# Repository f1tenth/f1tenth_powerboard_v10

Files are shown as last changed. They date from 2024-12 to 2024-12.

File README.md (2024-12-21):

# Powerboard v10

This is a repository containing the design files and user manual for the Powerboard v10.

Developed by a collaboration between Ambimat Electronics and the University of Pennsylvania.

To purchase, please order from this link: [Ambimat Electronics Powerboard Purchase Link](https://orders.ambimat.com/product/f1tenth-power-board/).

Please reach out to neel.shah@ambimat.com in case there is any issue with the website.

## Repository layout

### Explanation of important files/folders

- ```Powerboard_v10_1_User_Manual.pdf```: Contains a description of the capabilities of the board. 
  - Relevant to everyone looking to purchase, fabricate, or modify the existing design.
- ```hardware_design_files\```: Folder containing the bill of materials, schematics, PCB layout files for Altium, and manufacturing files (drill data, gerber files, and pick-and-place data).
    - Relevant if you want to get the board fabricated yourself.
- ```mechanical_specifications\```: Folder containing the mechanical drawings.
    - Relevant if you want to design a mount or any physical support for this powerboard.

### File layout
```
.
│   Powerboard_v10_1_User_Manual.pdf
│   README.md
│
├───hardware_design_files
│   │   BOM.xlsx
│   │   schematics.pdf
│   │
│   ├───layout
│   │       1. BD.SchDoc
│   │       2. Input Section.SchDoc
│   │       3. Buck Boost_19V.SchDoc
│   │       4. Buck Boost_12V.SchDoc
│   │       5. Buck_5V1A.SchDoc
│   │       6. Revision History.SchDoc
│   │       AE170_PDU_02.04.PcbDoc
│   │       AE170_PDU_02.04.PrjPcb
│   │
│   └───manufacturingData
│       │   PickAndPlaceData.csv.csv
│       │
│       ├───DrillData
│       │       AE170_PDU_02.04-RoundHoles.TXT
│       │       AE170_PDU_02.04-SlotHoles.TXT
│       │       AE170_PDU_02.04.DRL
│       │       AE170_PDU_02.04.DRR
│       │
│       └───GerberData
│               AE170_PDU_02.04.apr
│               AE170_PDU_02.04.G1
│               AE170_PDU_02.04.G2
│               AE170_PDU_02.04.GBL
│               AE170_PDU_02.04.GBO
│               AE170_PDU_02.04.GBP
│               AE170_PDU_02.04.GBS
│               AE170_PDU_02.04.GD1
│               AE170_PDU_02.04.GM1
│               AE170_PDU_02.04.GTL
│               AE170_PDU_02.04.GTO
│               AE170_PDU_02.04.GTP
│               AE170_PDU_02.04.GTS
│
└───mechanical_specifications
        diagram.DXF
        diagram.pdf
```

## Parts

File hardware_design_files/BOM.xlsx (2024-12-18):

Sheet: BOM_AE170_PDU_02.02
Sr.# | Quantity | Designator | Description | PCB Footprint | Manu Part Number | Manufacturer | Vendor-1 | Vendor-1 Part Number | Vendor-2 | Vendor-2 Part Number
1 | 12 | C1, C11, C19, C21, C24, C28, C36, C38, C41, C43, C45, C49 | CAP CER 0.1UF 100V X7R 0603 | 0603 | CC0603KRX7R0BB104 | YAGEO | DIGIKEY | 311-1523-1-ND | MOUSER
2 | 8 | C2, C3, C6, C7, C34, C35, C44, C48 | CAP CER 10UF 50V X5R 0805 | 0805 | GRM21BR61H106KE43L | Murata Electronics | DIGIKEY | 490-18663-1-ND | FARNELL
3 | 3 | C4, C5, C8 | CAP CER 10000PF 50V X7R 0603 | 0603 | CC0603KPX7R9BB103 | Yageo | DIGIKEY | 311-1572-1-ND | FARNELL
4 | 11 | C9, C10, C12, C17, C18, C26, C27, C29, C51, C52, C53 | CAP CER 47UF 25V X5R 1206 | 1206 | C3216X5R1E476M160AC | TDK Corporation | DIGIKEY | 445-8047-1-ND | FARNELL
5 | 2 | C13, C30 | CAP CER 0.015UF 50V X7R 0603 | 0603 | CL10B153KB8NNNC | Samsung Electro-Mechanics | DIGIKEY | 1276-1277-1-ND | FARNELL
6 | 1 | C14 | CAP CER 6800PF 50V X7R 0603 | 0603 | AC0603KPX7R9BB682 | YAGEO | DIgikey | 13-AC0603KPX7R9BB682CT-ND | Element14
7 | 2 | C15, C32 | CAP ALUM POLY 82UF 20% 35V SMD | 8.3 x 8.3 | 35SVPF82M | Panasonic | DIGIKEY | P16562CT-ND | FARNELL
8 | 1 | C20 | CAP CER 100PF 50V C0G/NP0 0805 | 0805 | 08055A101JAT2A | AVX Corporation | DIGIKEY | 478-1316-1-ND | FARNELL
9 | 1 | C22 | CAP CER 270PF 50V X7R 0603 | 0603 | CC0603KRX7R9BB271 | Yageo | DIgikey | 311-1185-1-ND | Element14
10 | 2 | C23, C40 | CAP CER 1UF 50V X7R 0603 | 0603 | CC0603KRX7R9BB105 | Yageo | DIGIKEY | 311-2082-1-ND | FARNELL
11 | 2 | C25, C42 | CAP CER 47PF 50V X7R 10% 0603 | 0603 | C0603C470K5RAC7867 | KEMET | DIGIKEY | 399-16402-1-ND | FARNELL
12 | 1 | C31 | CAP CER 10000PF 50V X7R 0402 | 0402 | CGA2B3X7R1H103K050BB | TDK Corporation | DIGIKEY | 445-6893-1-ND | FARNELL
13 | 1 | C37 | CAP CER 330PF 50V C0G/NPO 0805 | 0805 | CC0805JRNPO9BN331 | YAGEO | DIgikey | 311-1117-1-ND | Element14
14 | 1 | C39 | CAP CER 82PF 50V C0G/NPO 0603 | 0603 | CC0603JRNPO9BN820 | Yageo | DIGIKEY | 311-1068-1-ND | FARNELL
15 | 1 | C46 | CAP CER 47PF 50V C0G/NP0 0402 | 0402 | CL05C470JB5NNNC | Samsung Electro-Mechanics | DIGIKEY | 1276-1699-1-ND | FARNELL
16 | 1 | C47 | CAP CER 47UF 16V X5R 1210 | 1210 | GRM32ER61C476KE15L | Murata Electronics | DIGIKEY | 490-6539-1-ND | FARNELL
17 | 1 | C50 | CAP CER 0.033UF 10V X7R 0402 | 0402 | GRM155R71A333KA01D | Murata Electronics | DIGIKEY | 490-1315-1-ND | FARNELL
18 | 2 | D1, D3 | DIODE SCHOTTKY 50V 5A SMC | DO214AB | B550C-13-F | Diodes Incorporated | DIGI-KEY | B550C-FDICT-ND | MOUSER
19 | 2 | D2, D4 | TVS DIODE 20VWM 32.4VC DO214AC | DO214AC | SMAJ20CA | Littelfuse Inc. | DIGI-KEY | SMAJ20CALFCT-ND | MOUSER
20 | 2 | D5, D8 | DIODE SCHOTTKY 50V 5A SMC | DO214AB | B550C-13-F | Diodes Incorporated | DIGI-KEY | B550C-FDICT-ND | MOUSER
21 | 4 | D6, D7, D9, D10 | DIODE SCHOTTKY 60V 2A SOD123F | SOD123F | SS26FL | onsemi | DIGI-KEY | SS26FLCT-ND | MOUSER
22 | 6 | FB1, FB2, FB3, FB4, FB5, FB6 | FERRITE BEAD 120 OHM 0805 1LN | 0805 | ABUP00201209121Y00 | Pulse Electronics | Digikey | 553-ABUP00201209121Y00CT-ND
23 | 1 | J1 | CONN HEADER SMD 4POS 2MM | HEADER-4P_2.0MM | B4B-PH-SM4-TB | JST Sales America Inc. | DIGIKEY | 455-B4B-PH-SM4-TBCT-ND | FARNELL | sunrom 6334
24 | 1 | J2 | CONN HEADER SMD 6POS 1MM | HEADER 6P | BM06B-SRSS-TB | JST Sales America Inc. | DIGIKEY | 455-BM06B-SRSS-TBCT-ND | FARNELL
25 | 4 | J3, J4, J5, J6 | EURO BLOCK 2P | HEADER-2P_3.5MM | EBWA-02-A | Adam Tech | DIGIKEY | 2057-EBWA-02-A-ND | FARNELL
26 | 2 | J7, J10 | CONN PWR JACK 2.5X5.5MM SOLDER | TH 3P | PJ-050BH | CUI Inc | DIGIKEY | CP-050BH-ND | FARNELL | sunrom 7070
27 | 1 | J8 | CONN HEADER 9PS 2.54MM | 1x9 2.54MM HEADER |  |  | DIGIKEY |  |  | Local
28 | 1 | J9 | CONN HEADER VERT 4POS 2.5MM | HEADER-4P_2.5MM | B4B-XH-A | JST Sales America Inc. | DIGIKEY | 455-B4B-XH-A-ND | FARNELL | sunrom 5225
29 | 1 | L1 | FIXED IND 3.3UH 14A 8.2 MOHM SMD | 8479 | 7443340330 | Würth Elektronik | Digikey | 732-2165-1-ND
30 | 1 | L2 | FIXED IND 2.2UH 9.7A 14.5MOHM SM | 5553 | SRP5030CA-2R2M | Bourns Inc. | Digikey | SRP5030CA-2R2MCT-ND
31 | 1 | L3 | FIXED IND 10UH 5A 21 MOHM SMD | 12.7 X 12.7 | SRR1208-100ML | Bourns Inc. | Digikey | SRR1208-100MLCT-ND | MOUSER
32 | 3 | LED1, LED2, LED3 | LED BLUE CLEAR 3MM 470NM | 0603 | LB Q39G-L2N2-35-1 | OSRAM Opto Semiconductors Inc | DIGIKEY | 475-2816-1-ND | FARNELL | 1652110
33 | 2 | Q1, Q2 | MOSFET N-CH 30V 22A 6SON | 6-SON | CSD17571Q2 | Texas Instruments | DIGIKEY | 296-37193-1-ND
34 | 2 | Q3, Q7 | MOSFET N-CH 60V 50A 8VSON | 8-VSON | CSD18537NQ5A | Texas Instruments | DIGIKEY | 296-36455-1-ND
35 | 1 | Q4 | MOSFET N-CH 100V 14.4A 6WSON | 6-SON | CSD19538Q2 | Texas Instruments | DIGIKEY | 296-47322-1-ND
36 | 3 | Q5, Q6, Q8 | MOSFET N-CH 60V 60A 8VSON | 8-VSON | CSD18543Q3A | Texas Instruments | DIGIKEY | 296-47321-1-ND
37 | 2 | R1, R14 | RES SMD 2K OHM 5% 1/10W 0603 | 0603 | ERJ-3GEYJ202V | Panasonic | DIGIKEY | P2.0KGCT-ND | FARNELL
38 | 2 | R2, R15 | RES SMD 249K OHM 1% 1/10W 0603 | 0603 | AC0603FR-07249KL | Yageo | DIGIKEY | 13-AC0603FR-07249KLCT-ND | FARNELL
39 | 1 | R3 | RES 42.2K OHM 1% 1/10W 0603 | 0603 | RC0603FR-0742K2L | Yageo | DIGIKEY | 311-42.2KHRCT-ND | FARNELL
40 | 2 | R4, R17 | RES SMD 10 OHM 1% 1/10W 0603 | 0603 | CRCW060310R0FKEA | Vishay Dale | DIGIKEY | 541-10.0HCT-ND | FARNELL
41 | 1 | R5 | RES 453K OHM 1% 1/10W 0603 | 0603 | RC0603FR-07453KL | Yageo | DIGIKEY | 311-453KHRCT-ND | FARNELL
42 | 5 | R6, R9, R19, R22, R28 | RES SMD 10K OHM 5% 1/10W 0603 | 0603 | RC0603JR-0710KL | Yageo | DIGIKEY | 311-10KGRCT-ND | FARNELL
43 | 2 | R7, R20 | RES 93.1K OHM 1% 1/10W 0603 | 0603 | RC0603FR-0793K1L | YAGEO | DIGIKEY | 311-93.1KHRCT-ND | FARNELL
44 | 2 | R8, R21 | RES 23.2K OHM 1% 1/10W 0603 | 0603 | RC0603FR-0723K2L | YAGEO | DIGIKEY | 311-23.2KHRCT-ND | FARNELL
45 | 2 | R10, R23 | RES SMD 20K OHM 5% 1/10W 0603 | 0603 | CRCW060320K0JNEA | Vishay Dale | DIGIKEY | 541-20KGCT-ND | FARNELL
46 | 4 | R11, R13, R24, R26 | RES SMD 100 OHM 1% 1/10W 0603 | 0603 | CRCW0603100RFKEA | Vishay Dale | DIGIKEY | 541-100HCT-ND | FARNELL
47 | 1 | R12 | RES 0.01 OHM 1% 3W 2512 | 2512 | PA2512FKE7T0R01E | YAGEO | DIGIKEY | 13-PA2512FKE7T0R01ECT-ND | FARNELL
48 | 1 | R16 | RES SMD 33.2K OHM 1% 1/10W 0603 | 0603 | ERJ-3EKF3322V | Panasonic Electronic Components | DIGIKEY | P33.2KHCT-ND | FARNELL
49 | 1 | R18 | RES SMD 280K OHM 1% 1/10W 0603 | 0603 | CRCW0603280KFKEA | Vishay Dale | DIGIKEY | 541-280KHCT-ND | FARNELL
50 | 1 | R25 | RES 0.018 OHM 1W 1206 WIDE | 2012 | PRL1632-R018-F-T1 | Susumu | DIGIKEY | PRL1632.018FCT-ND | FARNELL
51 | 1 | R27 | RES 52.3K OHM 1% 1/10W 0603 | 0603 | RC0603FR-0752K3L | YAGEO | DIGIKEY | 311-52.3KHRCT-ND | FARNELL
52 | 3 | R30, R31, R32 | RES 470 OHM 1/10W 5% 0603 SMD | 0603 | RC0603JR-07470RL | YAGEO | DIGIKEY | 311-470GRCT-ND | MOUSER
53 | 2 | SW1, SW2 | SWITCH TOGGLE SPDT 7.5A 125V | E101SYZQE | E101SYZQE | C&K | DIGI-KEY | CKN1519-ND | MOUSER
54 | 2 | U1, U2 | LM5176PWPR | 28-HTSSOP | LM5176PWPR | Texas Instruments | DigiKey | 296-49223-1-ND | Element14
55 | 1 | U3 | IC REG BUCK ADJ 2A SOT583 | SOT-583 | TPS62932DRLR | Texas Instruments | DigiKey | 296-TPS62932DRLRCT-ND | MOUSER
 | 127

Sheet: DNP
Sr.# | Quantity | Designator | Description | PCB Footprint | Manu Part Number | Manufacturer | Vendor-1 | Vendor-1 Part Number | Vendor-2 | Vendor-2 Part Number | Mounting
1 | 2 | C16, C33 | CAP CER 22UF 35V X5R 0805 | 0805 | C2012X5R1V226M125AC | TDK Corporation | DIGIKEY | 445-14428-1-ND | FARNELL |  | DNP
2 | 1 | R29 | RES SMD 0 OHM JUMPER 1/10W 0603 | 0603 | CRCW06030000ZSTB | Vishay Dale | DIGIKEY | 541-2971-1-ND | FARNELL |  | DNP

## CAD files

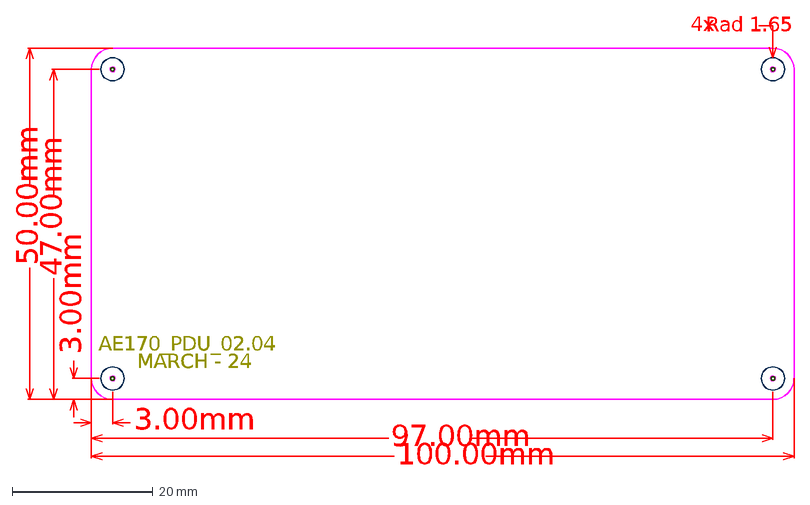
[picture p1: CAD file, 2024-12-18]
mechanical_specifications/diagram.DXF
4x
MARCH - 24
AE170_PDU_02.04
100.00mm
50.00mm
3.00mm
97.00mm
47.00mm
Rad 1.65

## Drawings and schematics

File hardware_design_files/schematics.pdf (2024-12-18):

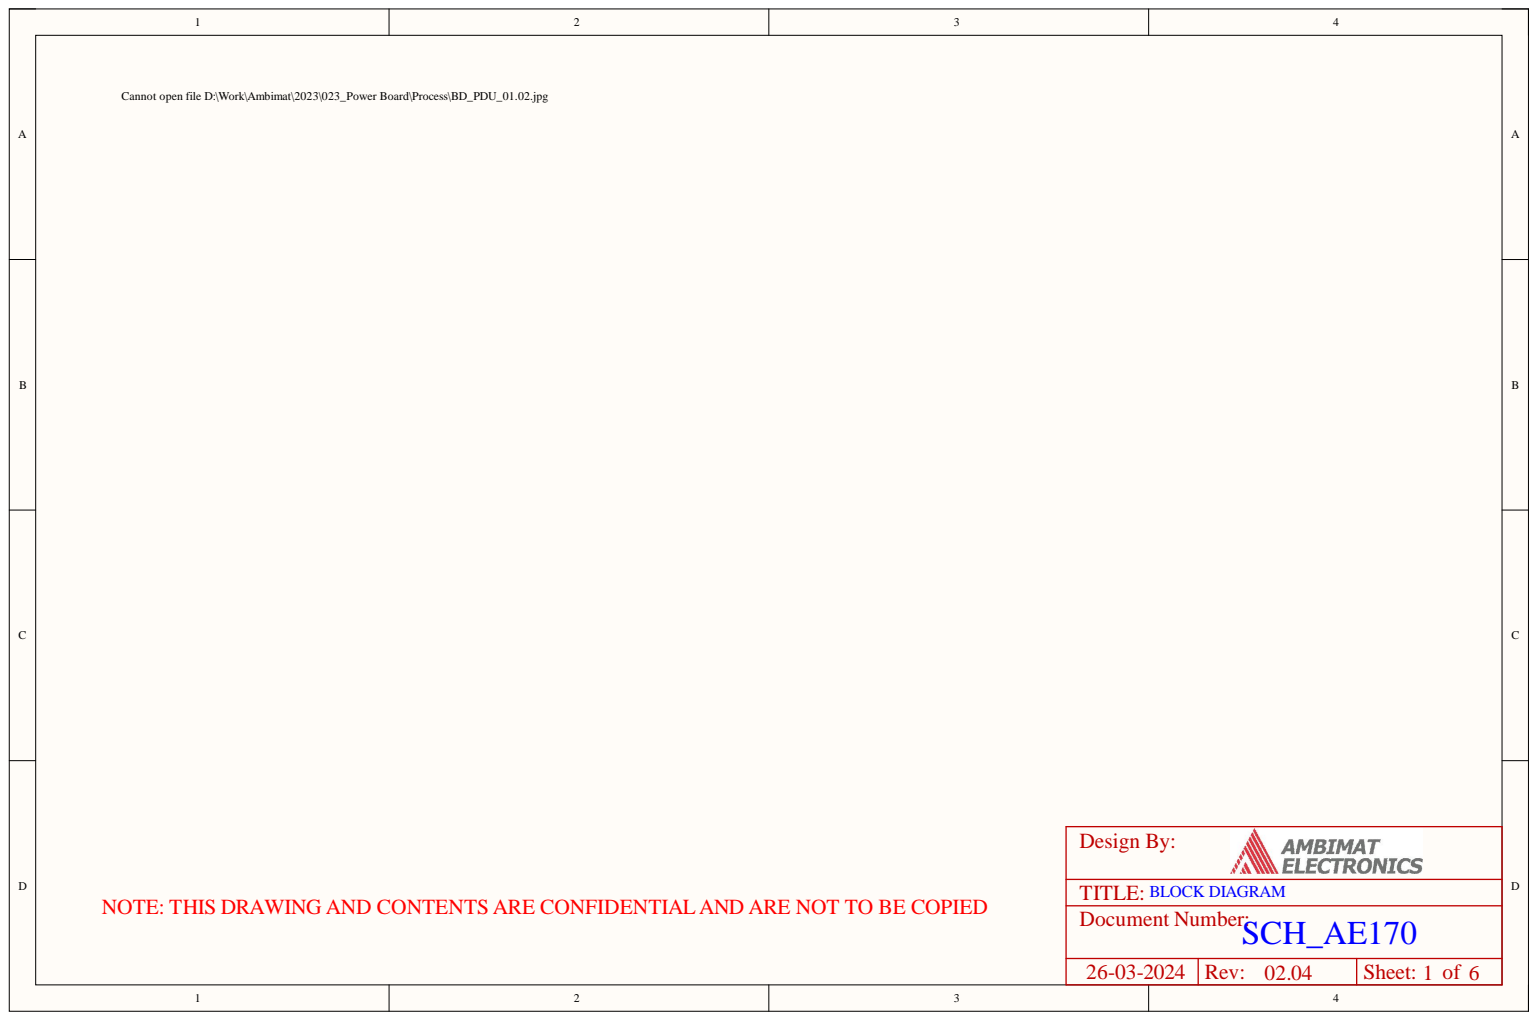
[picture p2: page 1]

Cannot open file D:\Work\Ambimat\2023\023_Power Board\Process\BD_PDU_01.02.jpg

NOTE: THIS DRAWING AND CONTENTS ARE CONFIDENTIALAND ARE NOT TO BE COPIED

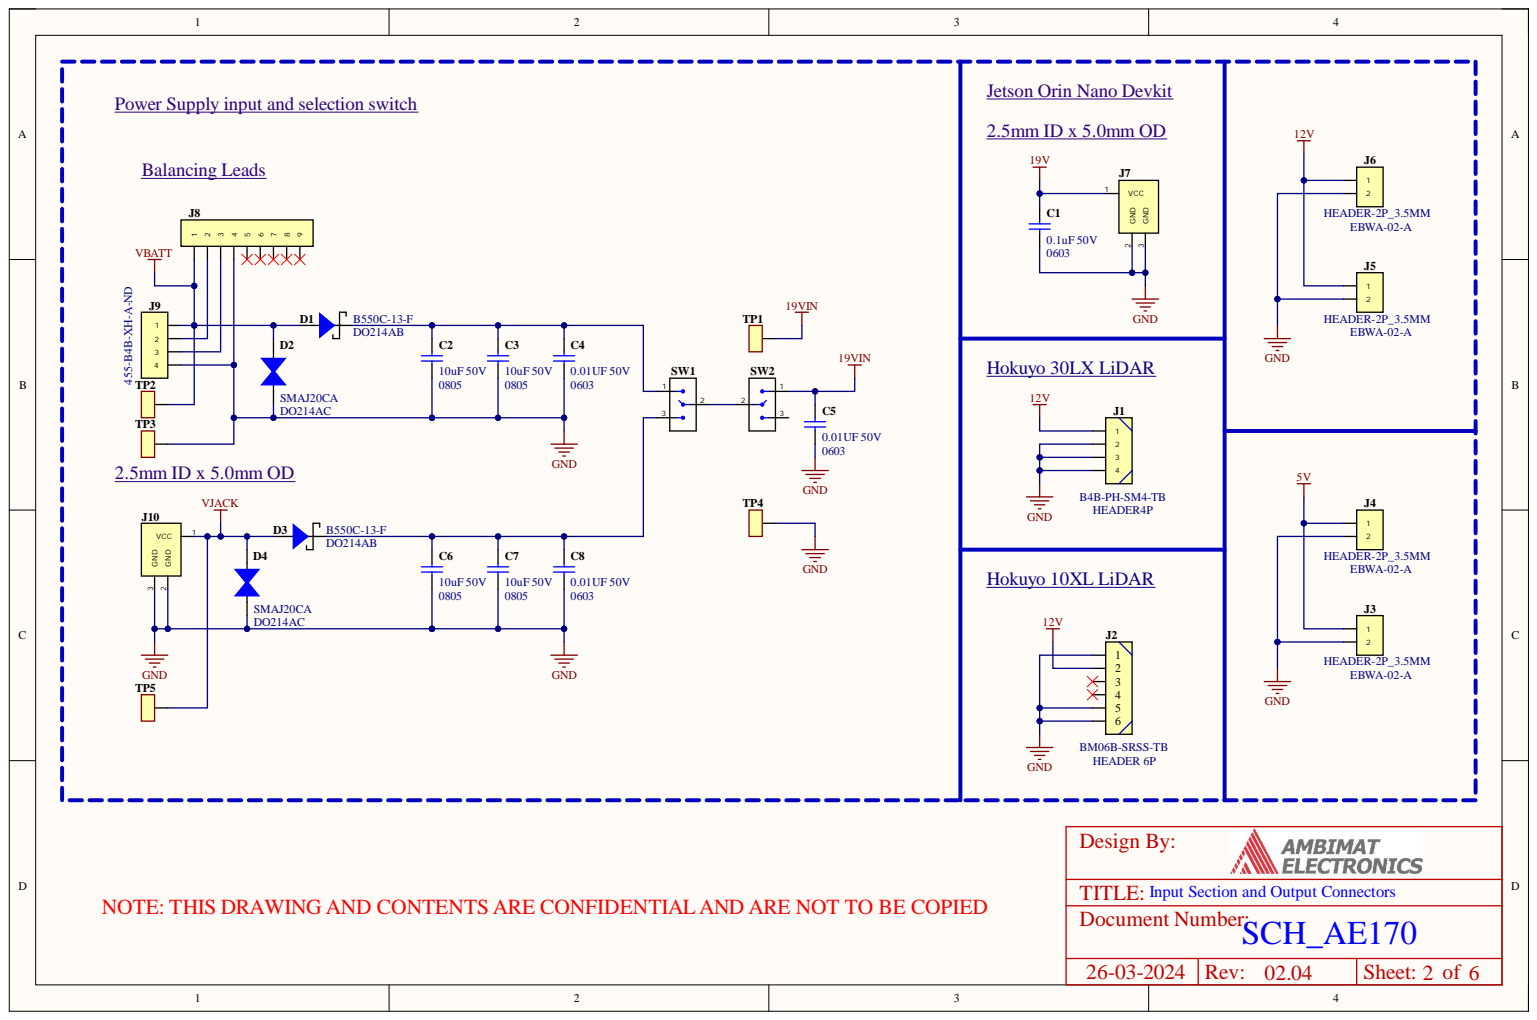
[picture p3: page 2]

ARE NOT TO BE COPIED

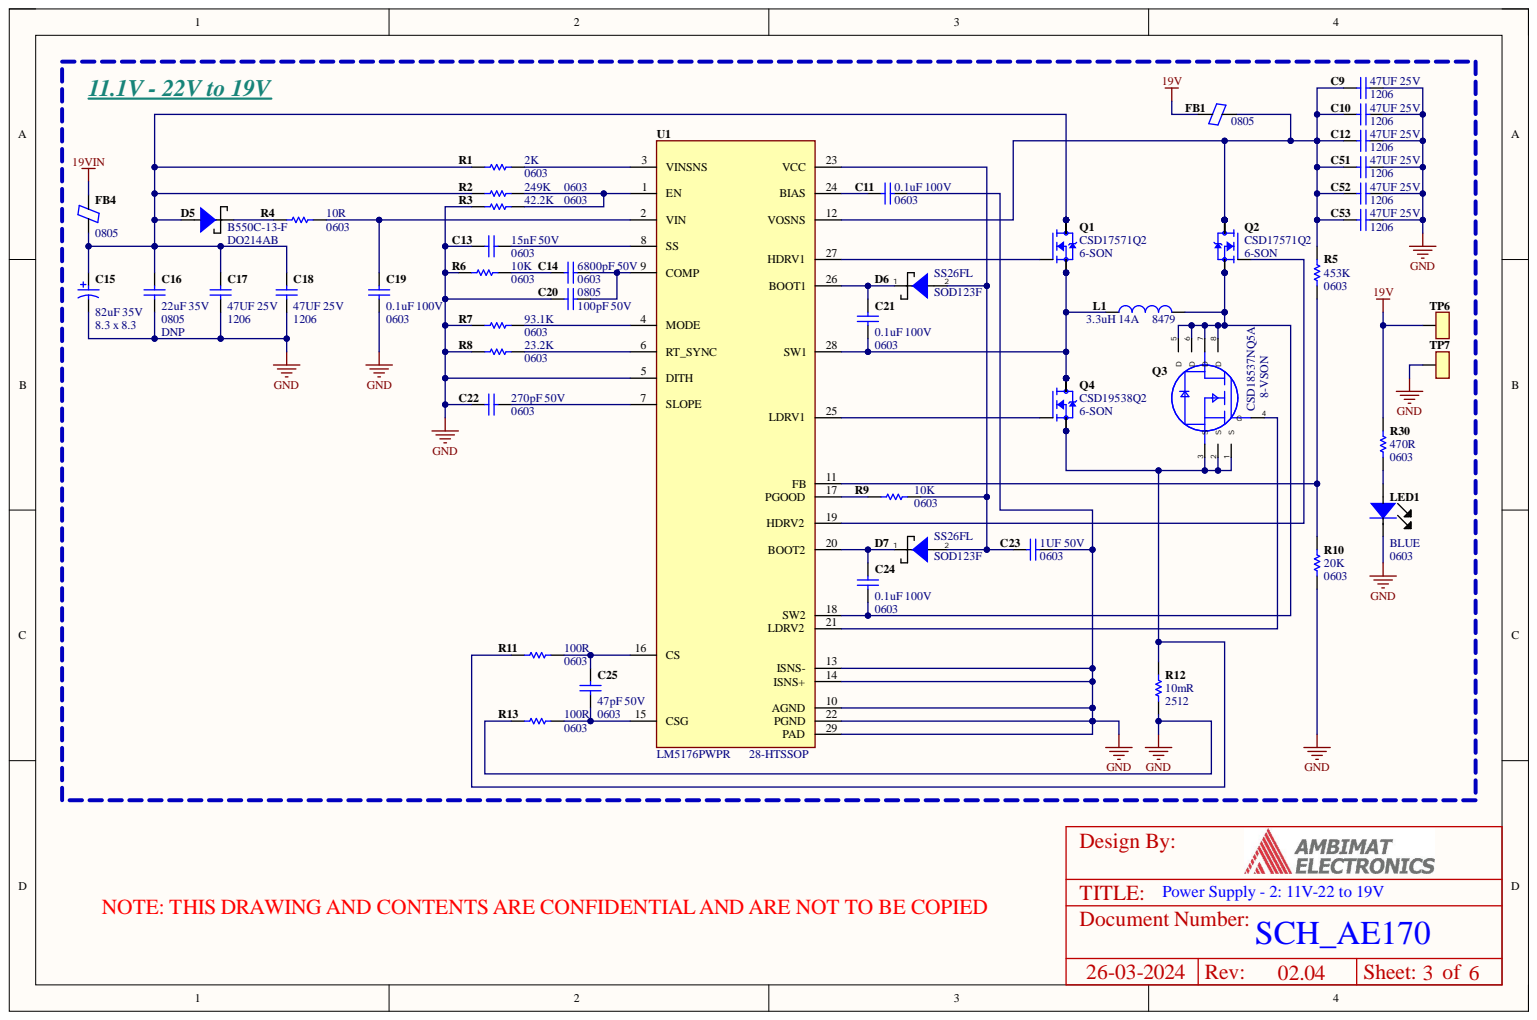
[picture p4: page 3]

2 6
2 8 | | SO D 1 2 3 F

1 1
1 7 | R 9 1 0 K
1 9 | 0 | 6 0 3

1 3
1 4

ARE NOT TO BE COPIED

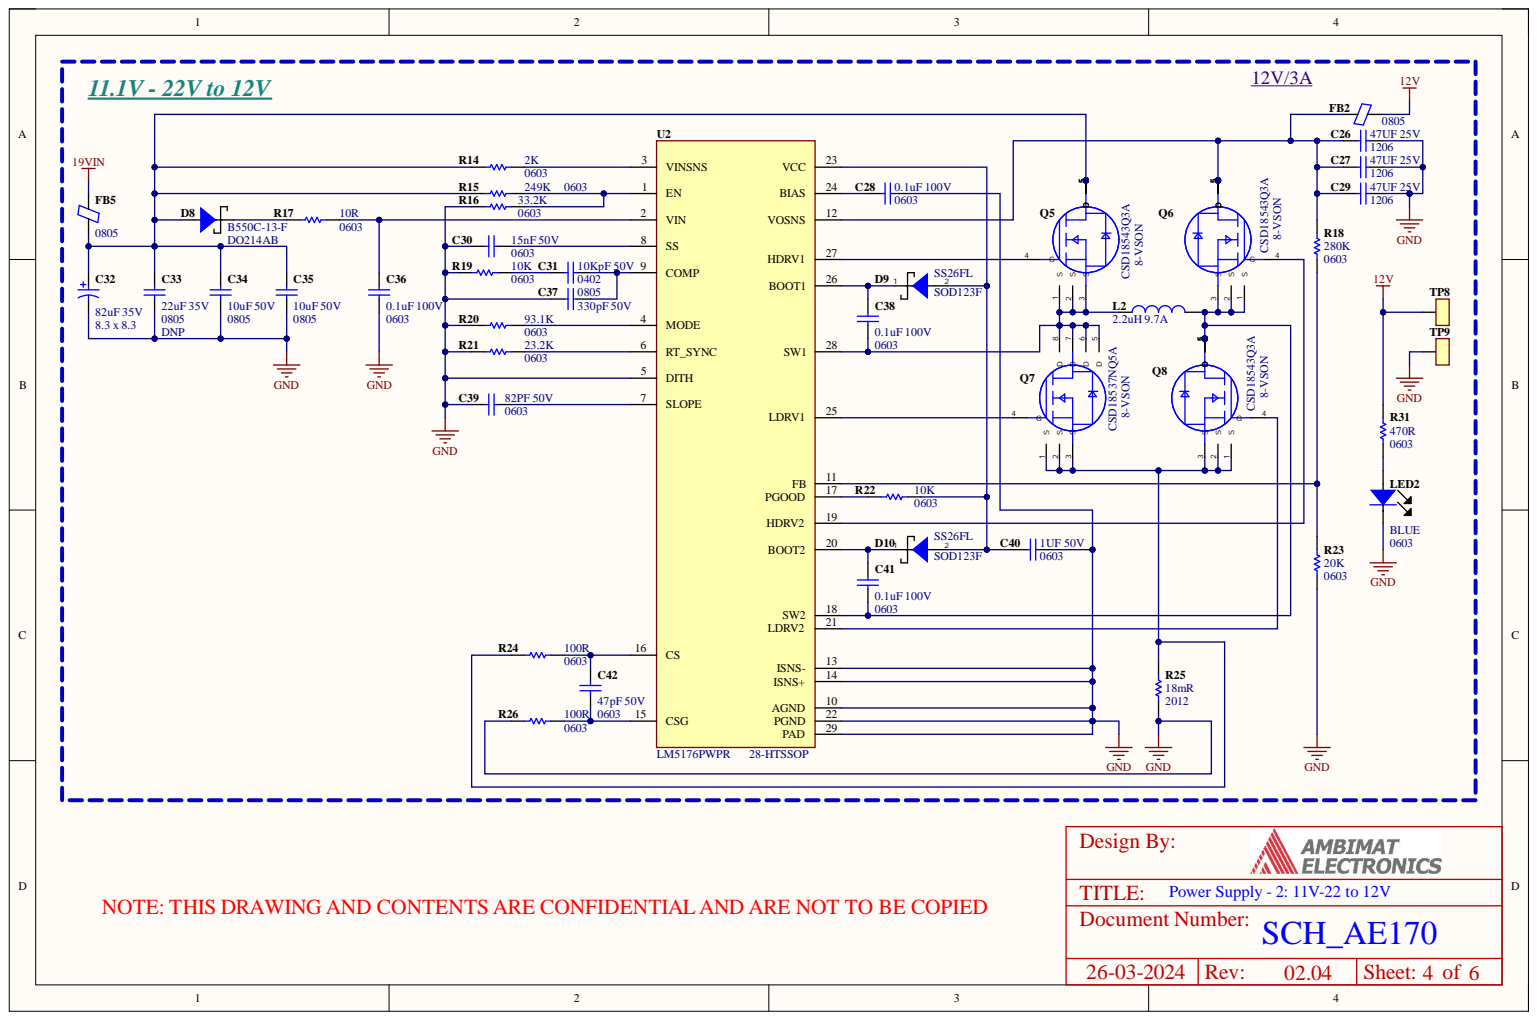
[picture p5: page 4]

1 1
1 7 | R 2 2 1 0 K
1 9 | 0 | 6 0 3

1 3
1 4

ARE NOT TO BE COPIED

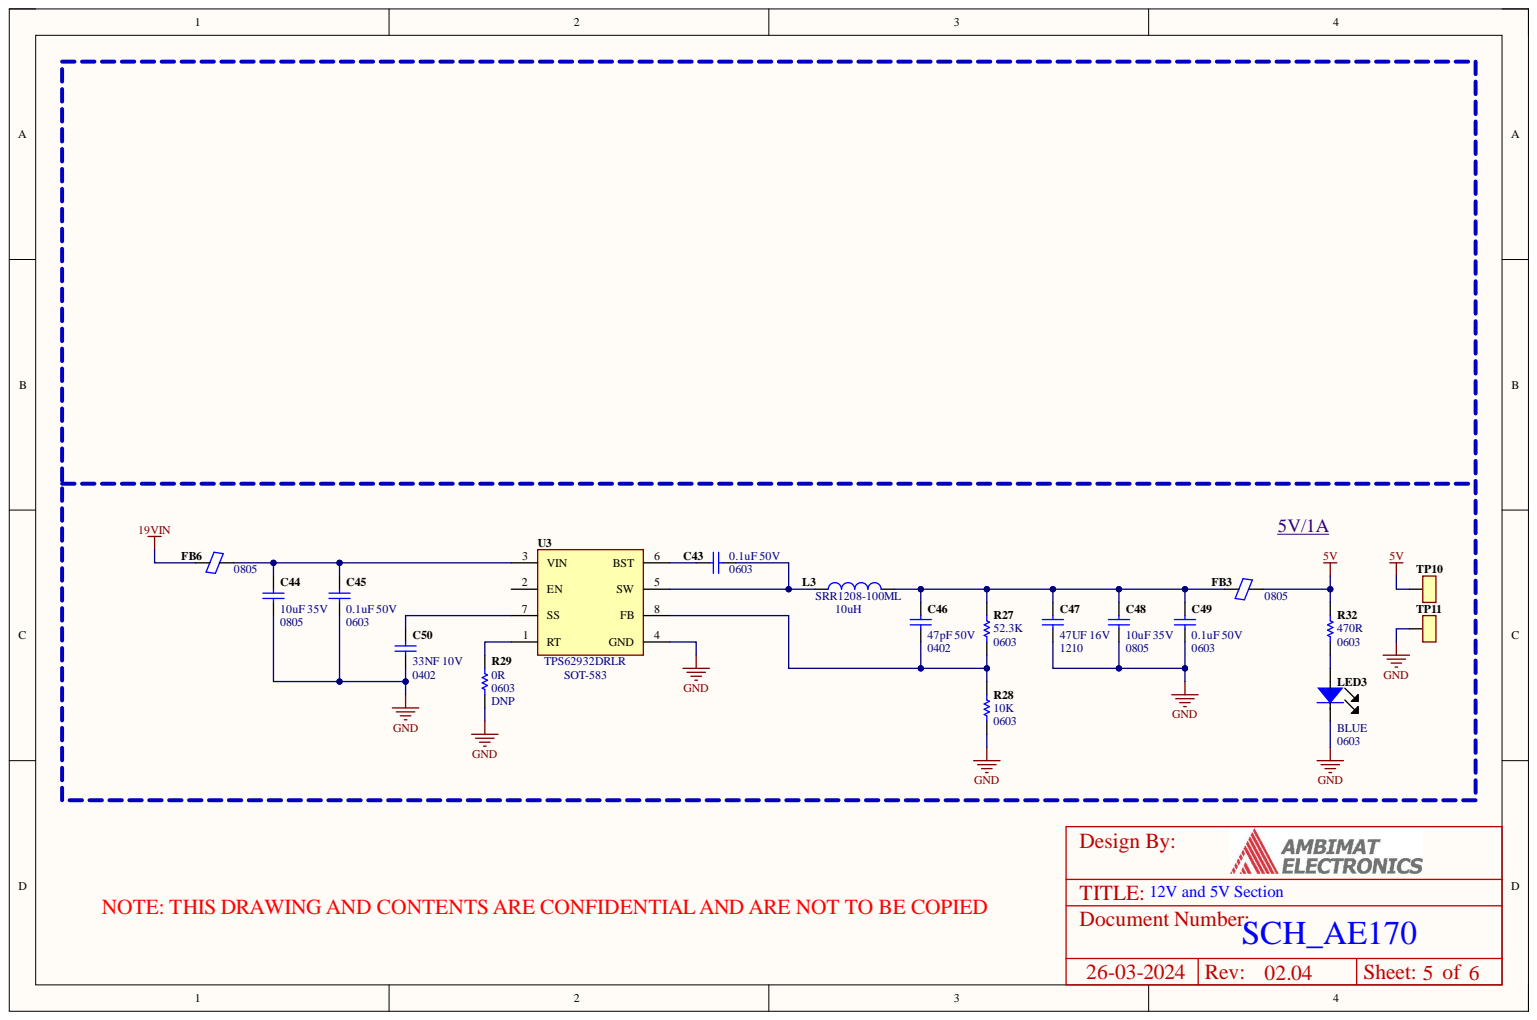
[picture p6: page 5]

ARE NOT TO BE COPIED

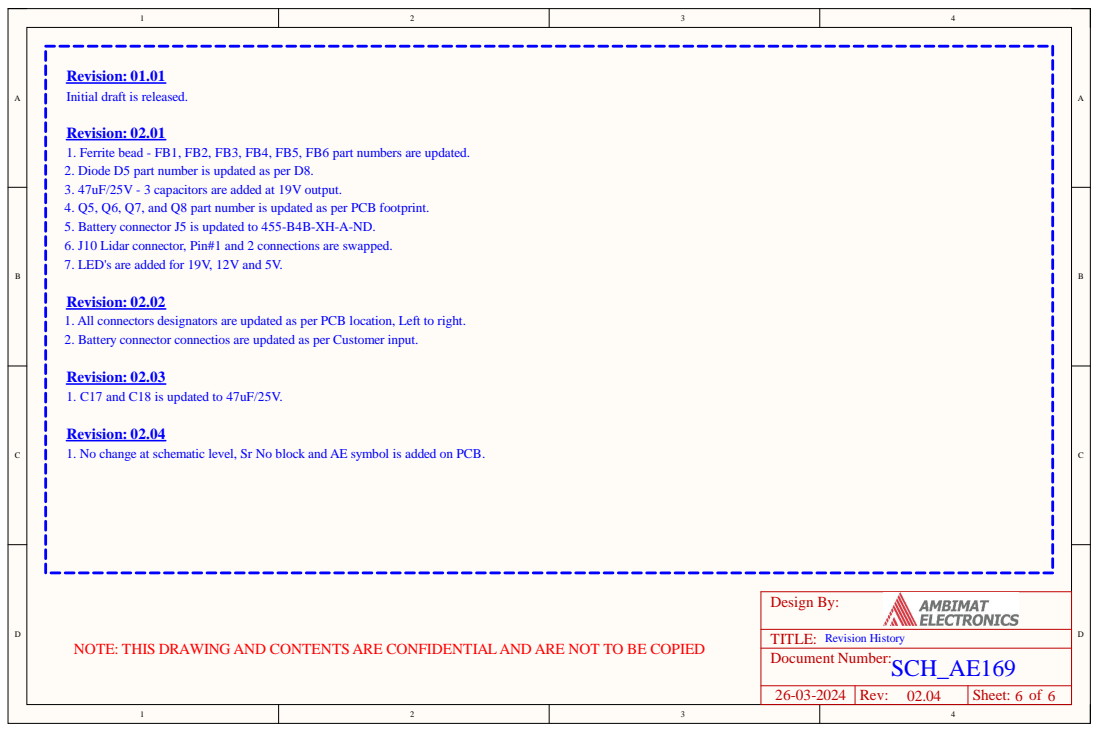
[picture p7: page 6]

Revision: 01.01
Initial draft is released.

Revision: 02.01
1. Ferrite bead - FB1, FB2, FB3, FB4, FB5, FB6 part numbers are updated.
2. Diode D5 part number is updated as per D8.
3. 47uF/25V - 3 capacitors are added at 19V output.
4. Q5, Q6, Q7, and Q8 part number is updated as per PCB footprint.
5. Battery connector J5 is updated to 455-B4B-XH-A-ND.
6. J10 Lidar connector, Pin#1 and 2 connections are swapped.
7. LED's are added for 19V, 12V and 5V.

Revision: 02.02
1. All connectors designators are updated as per PCB location, Left to right.
2. Battery connector connectios are updated as per Customer input.

Revision: 02.03
1. C17 and C18 is updated to 47uF/25V.

Revision: 02.04
1. No change at schematic level, Sr No block and AE symbol is added on PCB.

NOTE: THIS DRAWING AND CONTENTS ARE CONFIDENTIALAND ARE NOT TO BE COPIED

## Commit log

2024-12-18 added pick and place csv
    [AE170_PDU_02.04.DRL, AE170_PDU_02.04.GBL, AE170_PDU_02.04.GBO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]
2024-12-18 fixed typo in filename
    [PickAndPlaceData.csv]
